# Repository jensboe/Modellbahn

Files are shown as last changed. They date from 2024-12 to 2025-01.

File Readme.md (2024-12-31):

# System architecture
The `adapter board A` is connected to a nucleo 64 board.
The `adapter board A` provides a 
```mermaid
block-beta

columns 1
block:selfmade
    block:base
        columns 1
        nucleo
        adapter["adapter board A"]
    end
    space
    expansion_1["expansion board A 1"]
    space
    expansion_n["expansion board A n"]
    space
    expansion_b["expansion board B"]
    adapter     <--> expansion_1
    expansion_1   ----> expansion_n
    expansion_n  ----> expansion_b
    style expansion_b stroke:#333,stroke-dasharray: 5 5;
end
space
block:extern
    power_supply
    track_1
    switch_1_a
    switch_1_b
    track_x
    switch_y_a
    switch_y_b
end
power_supply --> adapter
expansion_1 --> track_1
expansion_1 --> switch_1_a
expansion_1 --> switch_1_b

expansion_n --> track_x
expansion_n --> switch_y_a
expansion_n --> switch_y_b
```
## Connection between expansion boards
Required Wires:
1. Drive Ground
2. Drive voltage
3. Switch voltage
4. Vcc (3V3 or 5V?)
5. D_Ground
6. MOSI
7. MISO
8. CLK

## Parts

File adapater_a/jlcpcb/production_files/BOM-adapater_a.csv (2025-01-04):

Comment | Designator | Footprint | LCSC | Quantity
CN7 | J104 | PinHeader_2x10_P2.54mm_Vertical | C124359 | 1
Jumper_3_Bridged12 | JP101,JP102,JP103,JP105,JP106 | PinHeader_1x03_P2.54mm_Vertical | C124376 | 5
100k | R301 | R_0805_2012Metric | C149504 | 1
10n | C106,C109,C110,C304,C305 | C_0805_2012Metric | C1710 | 5
1k2 | R102,R302,R303 | R_0805_2012Metric | C17379 | 3
10k | R101,R105,R106 | R_0805_2012Metric | C17414 | 3
150 | R108,R109,R110,R111 | R_0805_2012Metric | C17471 | 4
68k | R104,R112,R113 | R_0805_2012Metric | C17801 | 3
yl | D106 | LED_0805_2012Metric | C2296 | 1
gr | D104,D107 | LED_0805_2012Metric | C2297 | 2
820 | R107 | R_0805_2012Metric | C23253 | 1
0R1 | R103 | R_1206_3216Metric | C25334 | 1
CN10 | J105 | PinHeader_2x17_P2.54mm_Vertical | C2685134 | 1
TLV2372 | U102 | SOIC-8_3.9x4.9mm_P1.27mm | C27204 | 1
100n | C108,C303 | C_0805_2012Metric | C28233 | 2
10u | C105 | CP_Elec_6.3x5.4 | C29199 | 1
KBL406 | D101 | Diode_Bridge_Vishay_KBL | C3078 | 1
SW_DIP_x10 | SW101 | SW_DIP_SPSTx10_Slide_KingTek_DSHP10TS_W7.62mm_P1.27mm | C314500 | 1
220u | C107 | C_Elec_10x10.2 | C3358 | 1
100u | C302 | CP_Elec_6.3x5.4 | C37308 | 1
5n6 | C301 | C_0805_2012Metric | C56078 | 1
CN9 | J103 | PinHeader_2x15_P2.54mm_Vertical | C56496 | 1
B340 | D102,D103 | D_SMA | C64982 | 2
CN8 | J102 | PinHeader_2x08_P2.54mm_Vertical | C68234 | 1
1N4148W | D301,D302 | D_SOD-123 | C81598 | 2
red | D105 | LED_0805_2012Metric | C84256 | 1
4m7 | C101,C102,C103,C104 | CP_Radial_D18.0mm_P7.50mm | C92163 | 4
L6226 | U301 | UFQFPN-32-1EP_5x5mm_P0.5mm_EP3.5x3.5mm | C95357 | 1
Conn_01x03 | J101,J201 | TerminalBlock_4Ucon_1x03_P3.50mm_Vertical | C976557 | 2
Conn_01x06 | J202 | TerminalBlock_4Ucon_1x06_P3.50mm_Vertical | C976560 | 1
TPS5430DDA | U101 | TI_SO-PowerPAD-8_ThermalVias | C9864 | 1
47u | L101 | L_Ferrocore_DLG-0504 | C9889 | 1

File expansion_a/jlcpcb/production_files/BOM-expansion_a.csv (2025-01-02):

Comment | Designator | Footprint | LCSC | Quantity
Jumper_3_Bridged12 | JP1001,JP301,JP401,JP501,JP601,JP701,JP801,JP901 | PinHeader_1x03_P2.54mm_Vertical | C124376 | 8
1k2 | R1002,R302,R402,R502,R602,R702,R802,R902 | R_0805_2012Metric | C17379 | 8
120 | R1001,R301,R401,R501,R601,R701,R801,R901 | R_0805_2012Metric | C17437 | 8
74HC373 | U101 | SO-20_5.3x12.6mm_P1.27mm | C22374060 | 1
100n | C101,C102 | C_0805_2012Metric | C28233 | 2
LED | D1001,D301,D401,D501,D601,D701,D801,D901 | CP_EIA-3528-12_Kemet-T | C5246350 | 8
74HC595 | U102 | SOIC-16W_5.3x10.2mm_P1.27mm | C5947 | 1
GAQY212G1S | U1001,U301,U401,U501,U601,U701,U801,U901 | SO-4_4.4x3.9mm_P2.54mm | C7435108 | 8
Conn_01x03 | J1101,J201 | TerminalBlock_4Ucon_1x03_P3.50mm_Vertical | C976557 | 2
Conn_01x06 | J1102,J202 | TerminalBlock_4Ucon_1x06_P3.50mm_Vertical | C976560 | 2
Conn_01x08 | J101 | TerminalBlock_4Ucon_1x08_P3.50mm_Vertical | C976562 | 1

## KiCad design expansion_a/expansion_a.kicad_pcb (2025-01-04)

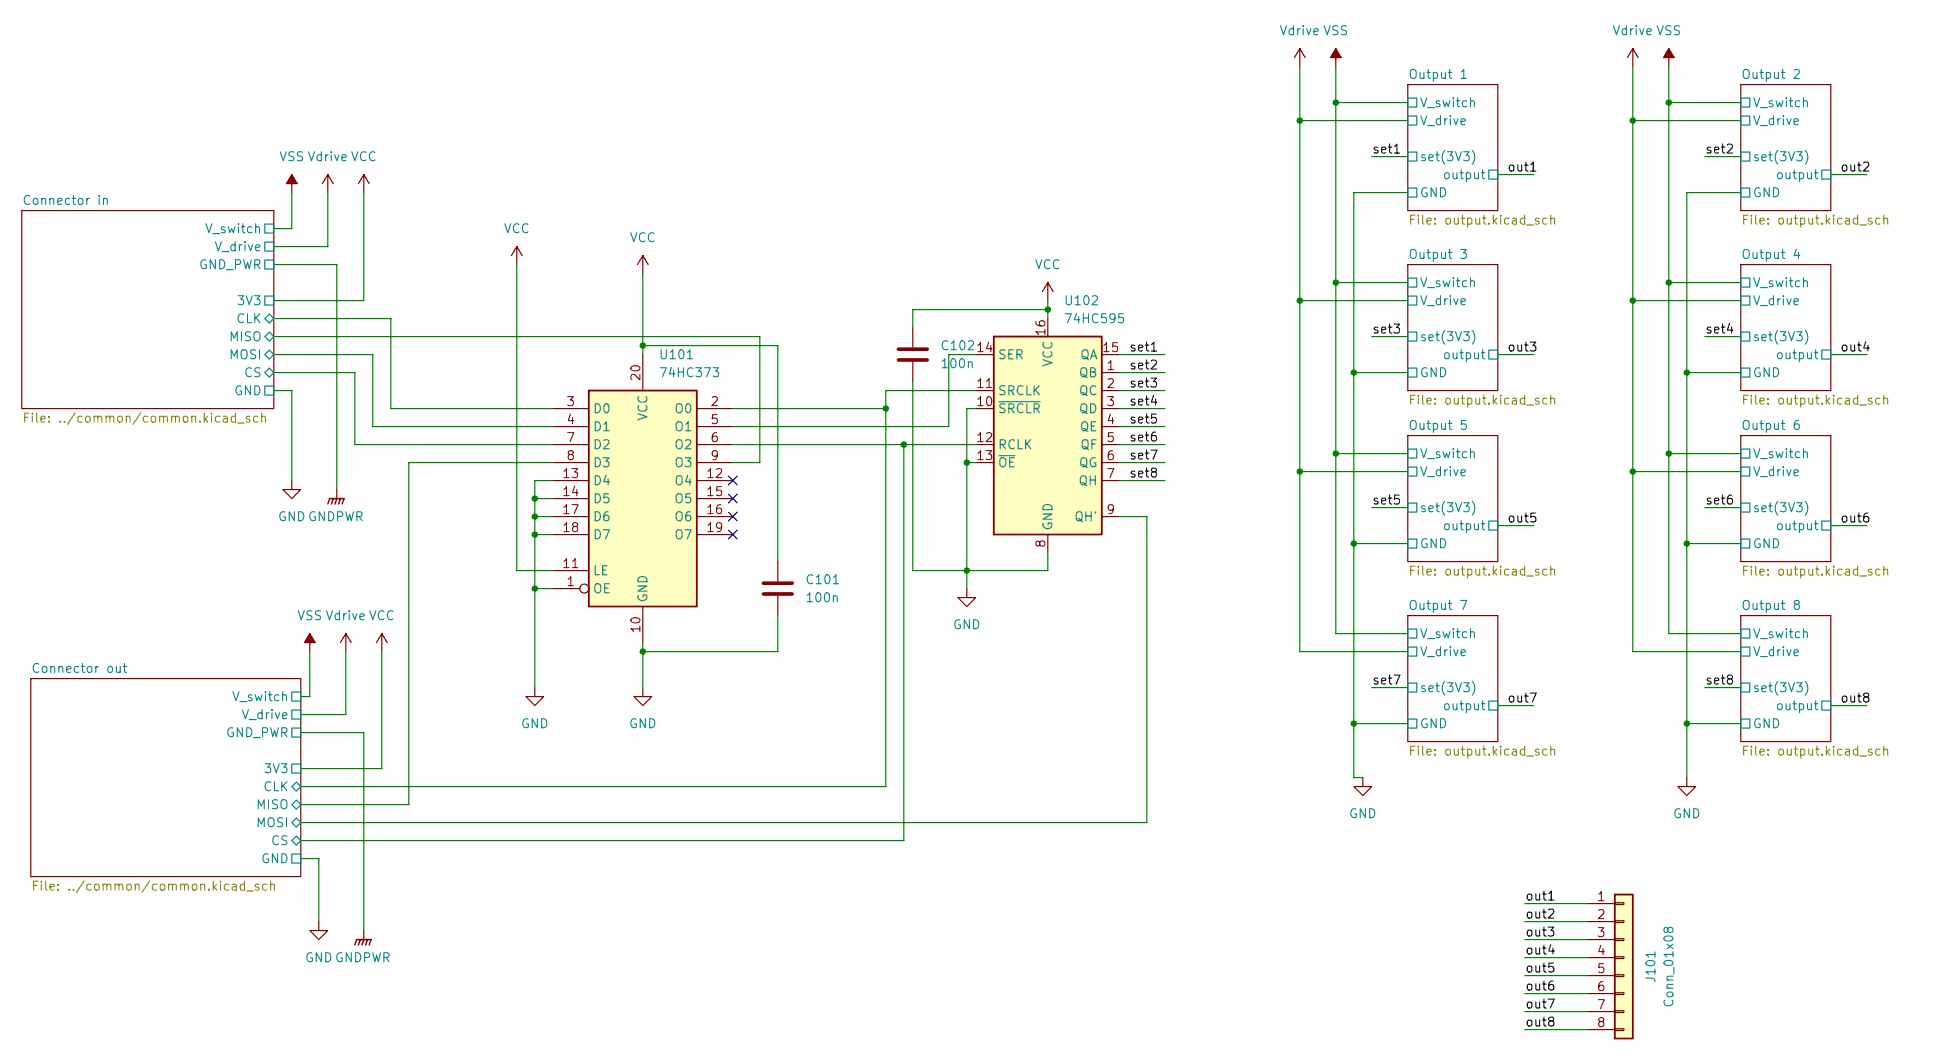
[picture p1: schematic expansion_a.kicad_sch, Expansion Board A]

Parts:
C101, C102: 100n; C_0805_2012Metric; LCSC C28233
J101: Conn_01x08; TerminalBlock_4Ucon_1x08_P3.50mm_Vertical; LCSC C976562
U101: 74HC373; SO-20_5.3x12.6mm_P1.27mm; LCSC C22374060
U102: 74HC595; SOIC-16W_5.3x10.2mm_P1.27mm; LCSC C5947

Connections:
/Connector in/CLK: U101.3 (D0); also elsewhere on the board
/Connector in/CS: U101.7 (D2); also elsewhere on the board
/Connector in/MISO: U101.9 (O3); also elsewhere on the board
/Connector in/MOSI: U101.4 (D1); also elsewhere on the board
/Connector out/CLK: U101.2 (O0), U102.11 (SRCLK); also elsewhere on the board
/Connector out/CS: U101.6 (O2), U102.12 (RCLK); also elsewhere on the board
/Connector out/MISO: U101.8 (D3); also elsewhere on the board
/Connector out/MOSI: U102.9 (QH'); also elsewhere on the board
/out1: J101.1; also elsewhere on the board
/out2: J101.2; also elsewhere on the board
/out3: J101.3; also elsewhere on the board
/out4: J101.4; also elsewhere on the board
/out5: J101.5; also elsewhere on the board
/out6: J101.6; also elsewhere on the board
/out7: J101.7; also elsewhere on the board
/out8: J101.8; also elsewhere on the board
/set1: U102.15 (QA); also elsewhere on the board
/set2: U102.1 (QB); also elsewhere on the board
/set3: U102.2 (QC); also elsewhere on the board
/set4: U102.3 (QD); also elsewhere on the board
/set5: U102.4 (QE); also elsewhere on the board
/set6: U102.5 (QF); also elsewhere on the board
/set7: U102.6 (QG); also elsewhere on the board
/set8: U102.7 (QH); also elsewhere on the board
GND: C101.2, C102.2, U101.1 (OE), U101.10 (GND), U101.13 (D4), U101.14 (D5), U101.17 (D6), U101.18 (D7), U102.8 (GND), U102.10 (~SRCLR), U102.13 (~OE); also elsewhere on the board
unnamed: U101.5 (O1), U102.14 (SER)
VCC: C101.1, C102.1, U101.11 (LE), U101.20 (VCC), U102.16 (VCC); also elsewhere on the board

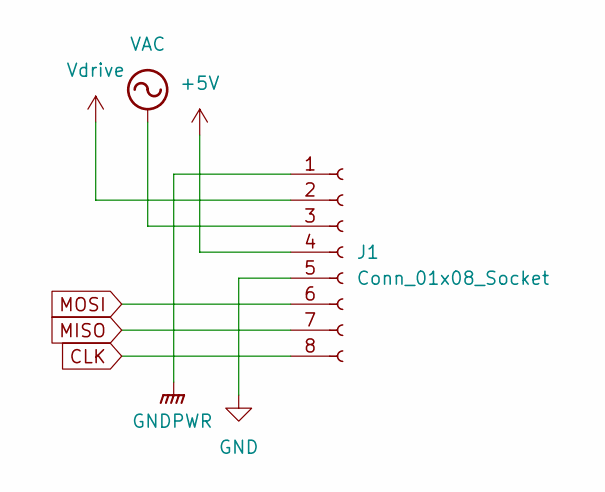
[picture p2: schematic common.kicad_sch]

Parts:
J1: Conn_01x08_Socket; TerminalBlock_4Ucon_1x08_P3.50mm_Vertical; LCSC C976562

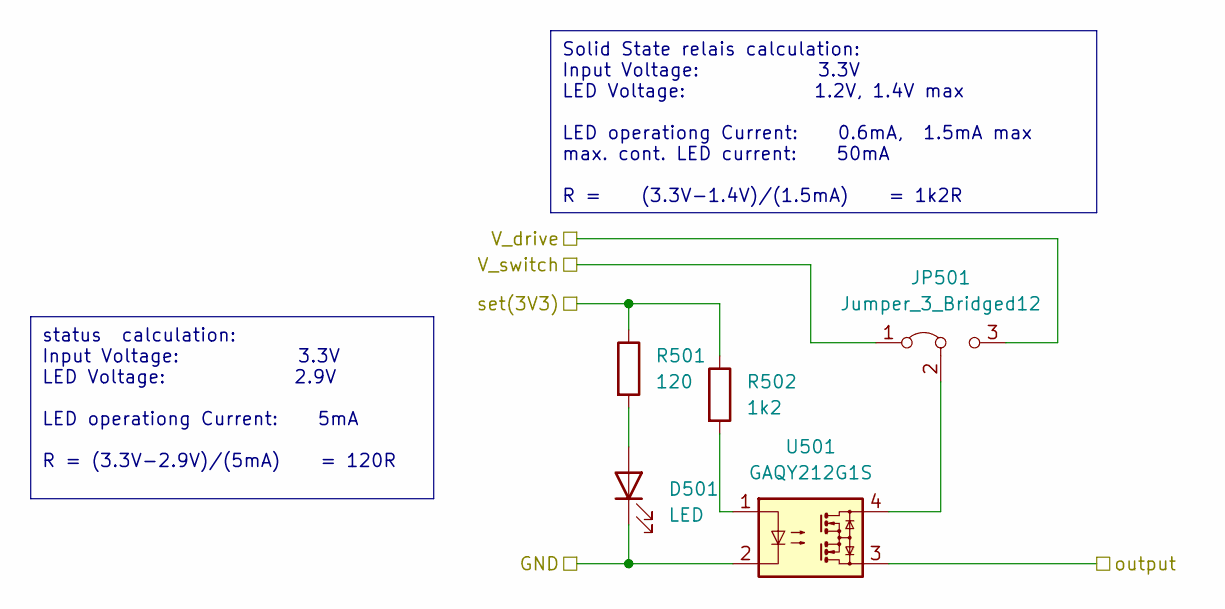
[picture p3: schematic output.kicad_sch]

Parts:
D501: LED; CP_EIA-3528-12_Kemet-T; LCSC C2290
JP501: Jumper_3_Bridged12; PinHeader_1x03_P2.54mm_Vertical; LCSC C124376
R501: 120; R_0805_2012Metric; LCSC C17437
R502: 1k2; R_0805_2012Metric; LCSC C17379
U501: GAQY212G1S; SO-4_4.4x3.9mm_P2.54mm; LCSC C7435108

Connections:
/out3: U501.3; also elsewhere on the board
/set3: R501.1, R502.1; also elsewhere on the board
GND: D501.1 (K), U501.2; also elsewhere on the board
unnamed: D501.2 (A), R501.2
unnamed: JP501.2 (C), U501.4
unnamed: R502.2, U501.1
VSS: JP501.1 (A); also elsewhere on the board
Vdrive: JP501.3 (B); also elsewhere on the board

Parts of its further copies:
D301, D401, D601, D701, D801, D901, D1001: LED; CP_EIA-3528-12_Kemet-T; LCSC C2290
JP301, JP401, JP601, JP701, JP801, JP901, JP1001: Jumper_3_Bridged12; PinHeader_1x03_P2.54mm_Vertical; LCSC C124376
R301, R401, R601, R701, R801, R901, R1001: 120; R_0805_2012Metric; LCSC C17437
R302, R402, R602, R702, R802, R902, R1002: 1k2; R_0805_2012Metric; LCSC C17379
U301, U401, U601, U701, U801, U901, U1001: GAQY212G1S; SO-4_4.4x3.9mm_P2.54mm; LCSC C7435108

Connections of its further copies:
/out1: U301.3; also elsewhere on the board
/out2: U401.3; also elsewhere on the board
/out4: U601.3; also elsewhere on the board
/out5: U701.3; also elsewhere on the board
/out6: U801.3; also elsewhere on the board
/out7: U901.3; also elsewhere on the board
/out8: U1001.3; also elsewhere on the board
/set1: R301.1, R302.1; also elsewhere on the board
/set2: R401.1, R402.1; also elsewhere on the board
/set4: R601.1, R602.1; also elsewhere on the board
/set5: R701.1, R702.1; also elsewhere on the board
/set6: R801.1, R802.1; also elsewhere on the board
/set7: R901.1, R902.1; also elsewhere on the board
/set8: R1001.1, R1002.1; also elsewhere on the board
GND: D301.1 (K), D401.1 (K), D601.1 (K), D701.1 (K), D801.1 (K), D901.1 (K), D1001.1 (K), U301.2, U401.2, U601.2, U701.2, U801.2, U901.2, U1001.2; also elsewhere on the board
unnamed: D301.2 (A), R301.2
unnamed: D401.2 (A), R401.2
unnamed: D601.2 (A), R601.2
unnamed: D701.2 (A), R701.2
unnamed: D801.2 (A), R801.2
unnamed: D901.2 (A), R901.2
unnamed: D1001.2 (A), R1001.2
unnamed: JP301.2 (C), U301.4
unnamed: JP401.2 (C), U401.4
unnamed: JP601.2 (C), U601.4
unnamed: JP701.2 (C), U701.4
unnamed: JP801.2 (C), U801.4
unnamed: JP901.2 (C), U901.4
unnamed: JP1001.2 (C), U1001.4
unnamed: R302.2, U301.1
unnamed: R402.2, U401.1
unnamed: R602.2, U601.1
unnamed: R702.2, U701.1
unnamed: R802.2, U801.1
unnamed: R902.2, U901.1
unnamed: R1002.2, U1001.1
VSS: JP301.1 (A), JP401.1 (A), JP601.1 (A), JP701.1 (A), JP801.1 (A), JP901.1 (A), JP1001.1 (A); also elsewhere on the board
Vdrive: JP301.3 (B), JP401.3 (B), JP601.3 (B), JP701.3 (B), JP801.3 (B), JP901.3 (B), JP1001.3 (B); also elsewhere on the board

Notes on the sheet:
Solid State relais calculation: Input Voltage: 3.3V LED Voltage: 1.2V, 1.4V max LED operationg Current: 0.6mA, 1.5mA max max. cont. LED current: 50mA R = (3.3V-1.4V)/(1.5mA) = 1k2R
status calculation: Input Voltage: 3.3V LED Voltage: 2.9V LED operationg Current: 5mA R = (3.3V-2.9V)/(5mA) = 120R

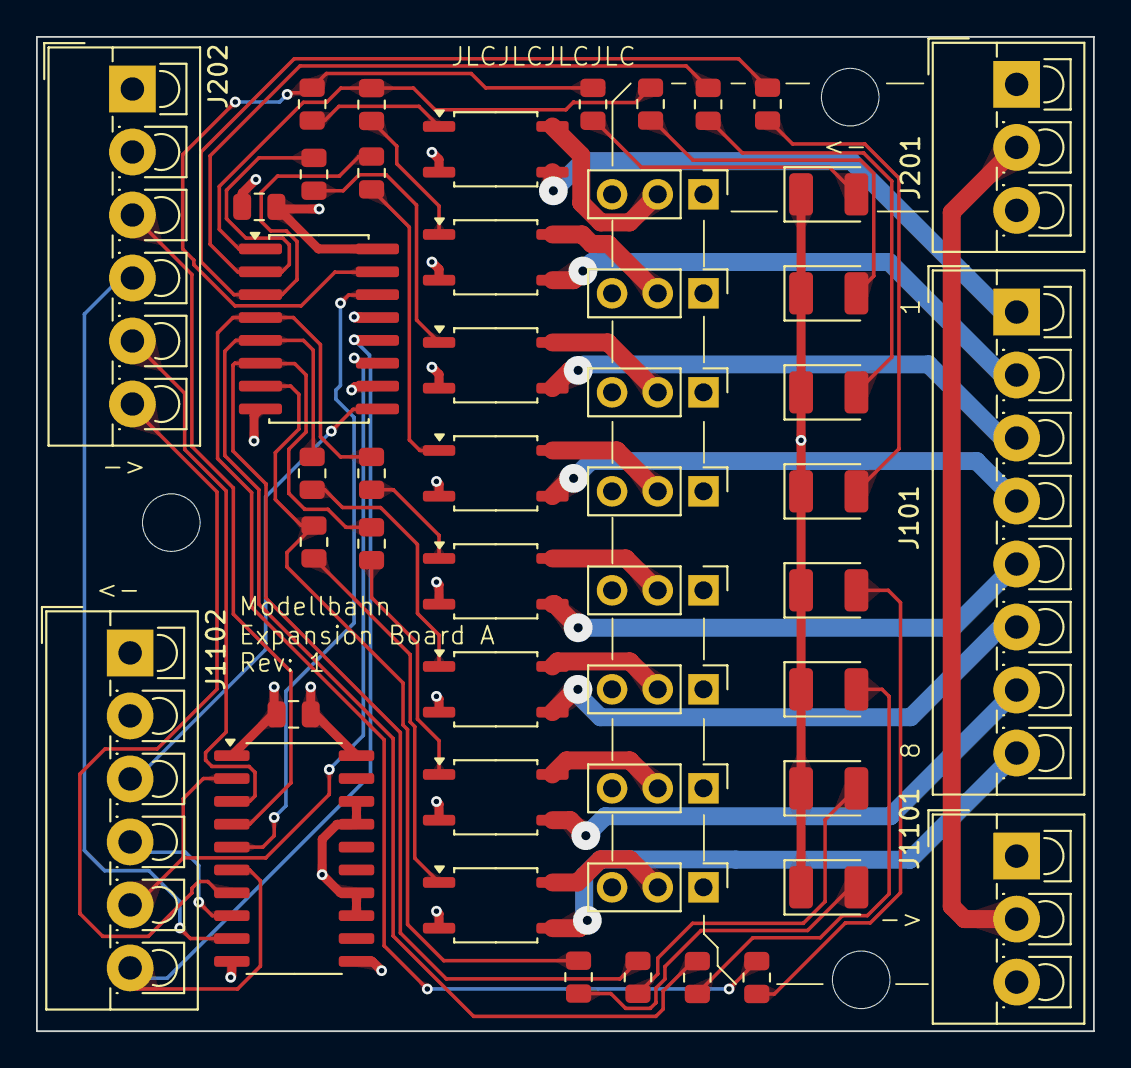
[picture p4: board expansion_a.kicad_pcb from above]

Board: 4 copper layers, 58.7 x 55.2 mm, 52 parts (0 on the bottom side), 54 nets.

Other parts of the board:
J201, J1101: Conn_01x03; TerminalBlock_4Ucon_1x03_P3.50mm_Vertical
J202, J1102: Conn_01x06; TerminalBlock_4Ucon_1x06_P3.50mm_Vertical
REF1, REF2, REF3: MountingHole_3.2mm_M3

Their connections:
/Connector in/CLK: J202.5; also elsewhere on the board
/Connector in/CS: J202.6; also elsewhere on the board
/Connector in/MISO: J202.4; also elsewhere on the board
/Connector in/MOSI: J202.3; also elsewhere on the board
/Connector out/CLK: J1102.5; also elsewhere on the board
/Connector out/CS: J1102.6; also elsewhere on the board
/Connector out/MISO: J1102.4; also elsewhere on the board
/Connector out/MOSI: J1102.3; also elsewhere on the board
GND: J202.2, J1102.2; also elsewhere on the board
GNDPWR: J201.2, J1101.2
VCC: J202.1, J1102.1; also elsewhere on the board
VSS: J201.3, J1101.3; also elsewhere on the board
Vdrive: J201.1, J1101.1; also elsewhere on the board

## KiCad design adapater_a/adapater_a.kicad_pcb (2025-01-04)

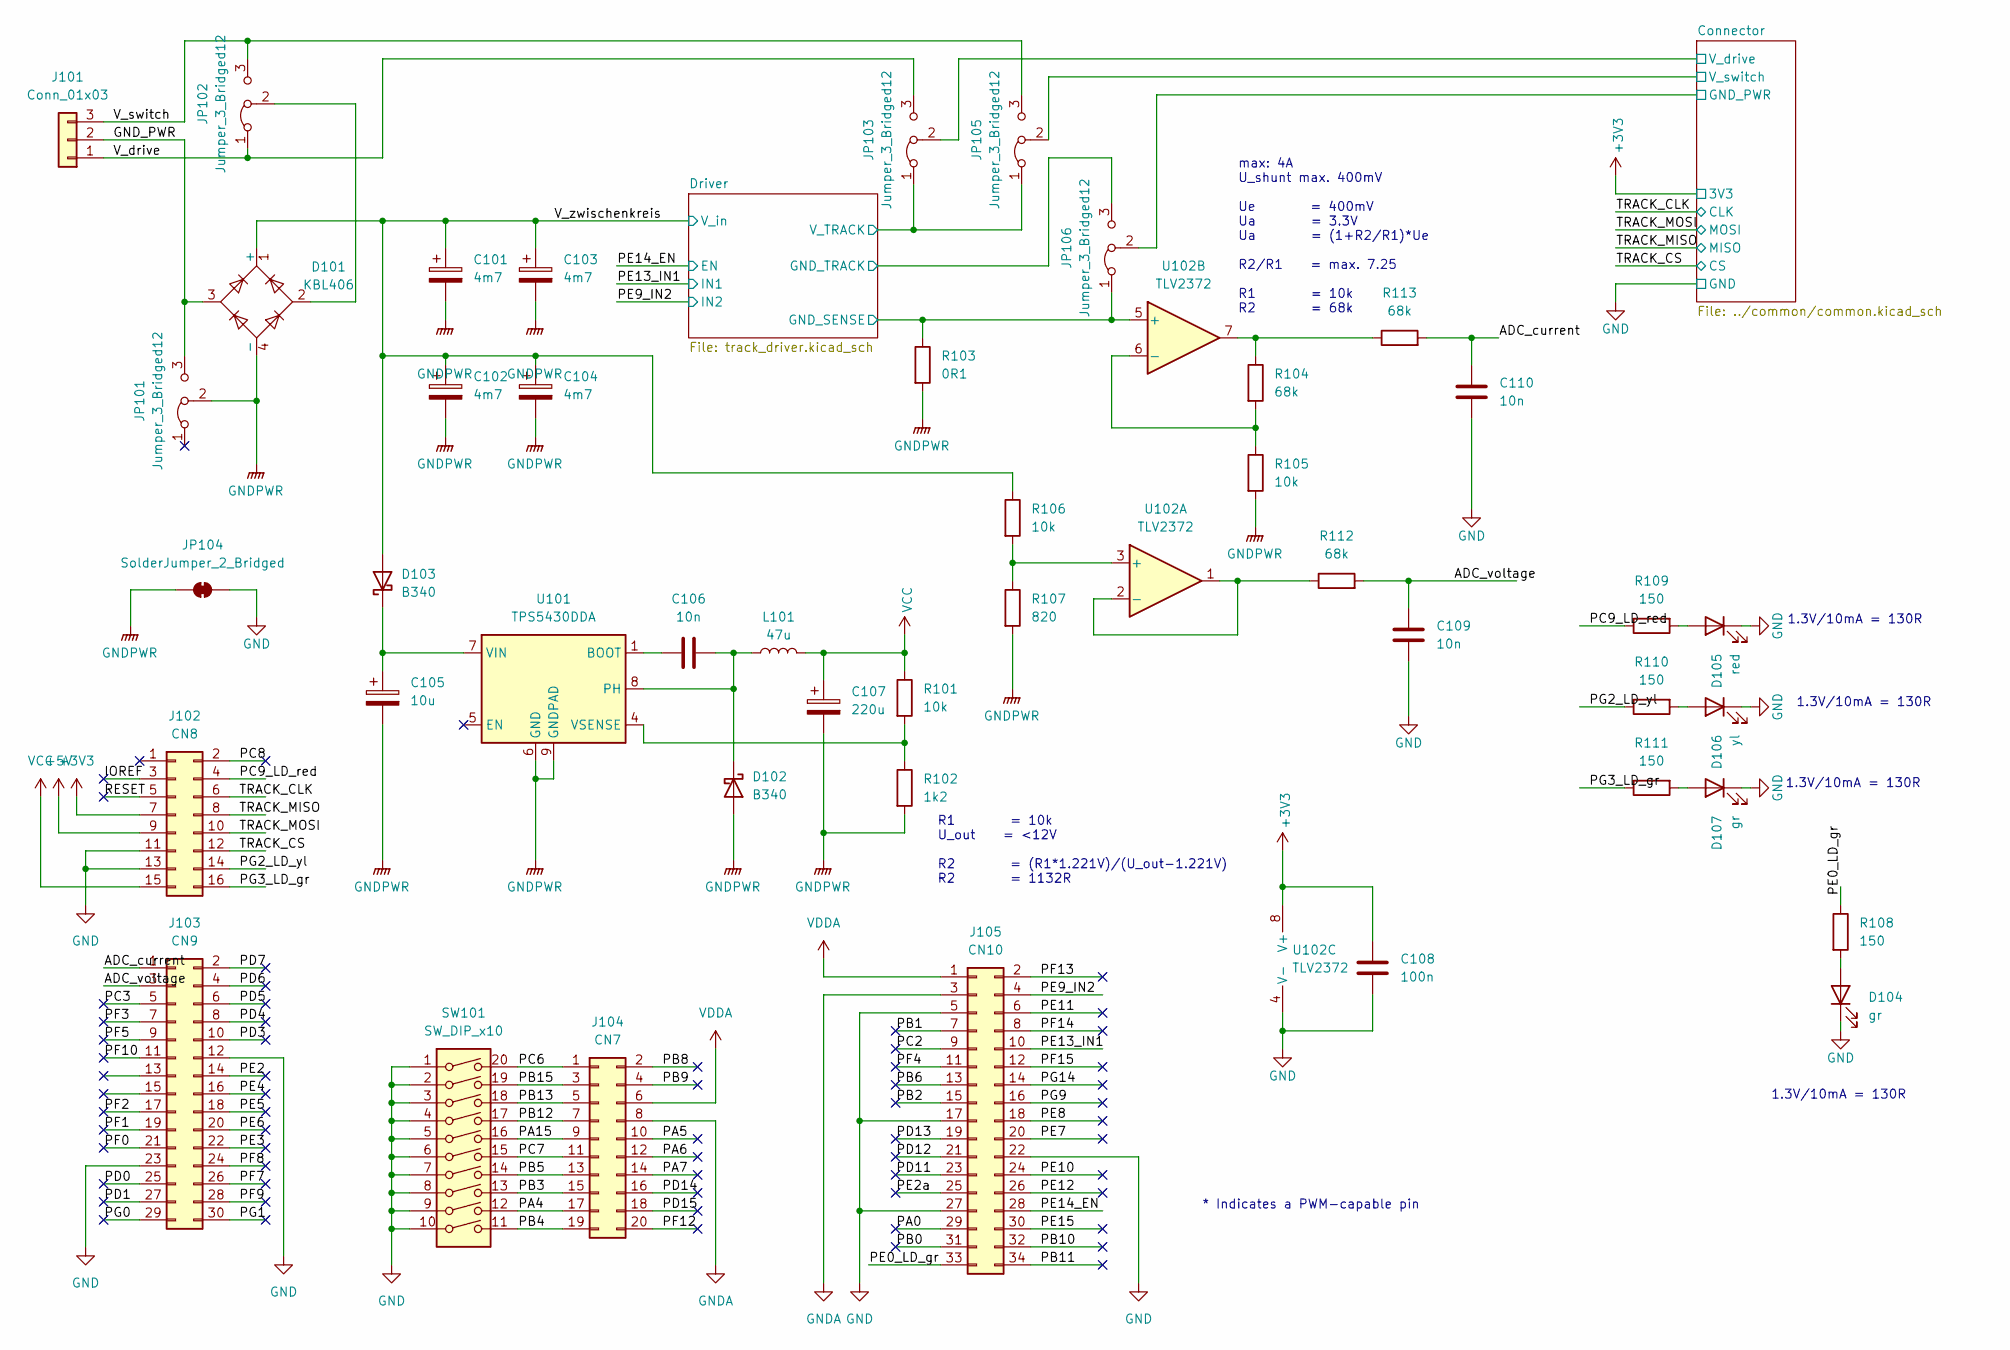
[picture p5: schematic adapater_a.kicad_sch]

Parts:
C101, C102, C103, C104: 4m7; CP_Radial_D18.0mm_P7.50mm; LCSC C92163
C105: 10u; CP_Elec_6.3x5.4; LCSC C29199
C106, C109, C110: 10n; C_0805_2012Metric; LCSC C1710
C107: 220u; C_Elec_10x10.2; LCSC C3358
C108: 100n; C_0805_2012Metric; LCSC C28233
D101: KBL406; Diode_Bridge_Vishay_KBL; LCSC C3078
D102, D103: B340; D_SMA; LCSC C64982
D104, D107: gr; LED_0805_2012Metric; LCSC C2297
D105: red; LED_0805_2012Metric; LCSC C84256
D106: yl; LED_0805_2012Metric; LCSC C2296
J101: Conn_01x03; TerminalBlock_4Ucon_1x03_P3.50mm_Vertical; LCSC C976557
J102: CN8; PinHeader_2x08_P2.54mm_Vertical; LCSC C68234
J103: CN9; PinHeader_2x15_P2.54mm_Vertical; LCSC C56496
J104: CN7; PinHeader_2x10_P2.54mm_Vertical; LCSC C5116480
J105: CN10; PinHeader_2x17_P2.54mm_Vertical; LCSC C2685134
JP101, JP102, JP103, JP105, JP106: Jumper_3_Bridged12; PinHeader_1x03_P2.54mm_Vertical; LCSC C124376
JP104: SolderJumper_2_Bridged; SolderJumper-2_P1.3mm_Bridged_RoundedPad1.0x1.5mm
L101: 47u; L_Ferrocore_DLG-0504; LCSC C9889
R101, R105, R106: 10k; R_0805_2012Metric; LCSC C17414
R102: 1k2; R_0805_2012Metric; LCSC C17379
R103: 0R1; R_1206_3216Metric; LCSC C25334
R104, R112, R113: 68k; R_0805_2012Metric; LCSC C17801
R107: 820; R_0805_2012Metric; LCSC C23253
R108, R109, R110, R111: 150; R_0805_2012Metric; LCSC C17471
SW101: SW_DIP_x10; SW_DIP_SPSTx10_Slide_KingTek_DSHP10TS_W7.62mm_P1.27mm; LCSC C314500
U101: TPS5430DDA; TI_SO-PowerPAD-8_ThermalVias; LCSC C9864
U102: TLV2372; SOIC-8_3.9x4.9mm_P1.27mm; LCSC C27204

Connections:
+3V3: C108.1, J102.7, U102.8 (V+); also elsewhere on the board
+5V: J102.9
/ADC_current: C110.2, J103.1, R113.2
/ADC_voltage: C109.2, J103.3, R112.2
/Connector/GND_PWR: JP106.2 (C); also elsewhere on the board
/Connector/V_drive: JP103.2 (C); also elsewhere on the board
/Connector/V_switch: JP105.2 (C); also elsewhere on the board
/Driver/GND_SENSE: JP106.1 (A), R103.1, U102.5 (+); also elsewhere on the board
/Driver/GND_TRACK: JP106.3 (B); also elsewhere on the board
/Driver/V_TRACK: JP103.1 (A), JP105.1 (A); also elsewhere on the board
/GND_PWR: D101.3, J101.2, JP101.3 (B)
/IOREF: J102.3
/PA0: J105.29
/PA4: J104.17, SW101.12
/PA5: J104.10
/PA6: J104.12
/PA7: J104.14
/PA15: J104.9, SW101.16
/PB0: J105.31
/PB1: J105.7
/PB2: J105.15
/PB3: J104.15, SW101.13
/PB4: J104.19, SW101.11
/PB5: J104.13, SW101.14
/PB6: J105.13
/PB8: J104.2
/PB9: J104.4
/PB10: J105.32
/PB11: J105.34
/PB12: J104.7, SW101.17
/PB13: J104.5, SW101.18
/PB15: J104.3, SW101.19
/PC2: J105.9
/PC3: J103.5
/PC6: J104.1, SW101.20
/PC7: J104.11, SW101.15
/PC8: J102.2
/PC9_LD_red: J102.4, R109.1
/PD0: J103.25
/PD1: J103.27
/PD3: J103.10
/PD4: J103.8
/PD5: J103.6
/PD6: J103.4
/PD7: J103.2
/PD11: J105.23
/PD12: J105.21
/PD13: J105.19
/PD14: J104.16
/PD15: J104.18
/PE0_LD_gr: J105.33, R108.1
/PE2: J103.14
/PE2a: J105.25
/PE3: J103.22
/PE4: J103.16
/PE5: J103.18
/PE6: J103.20
/PE7: J105.20
/PE8: J105.18
/PE9_IN2: J105.4; also elsewhere on the board
/PE10: J105.24
/PE11: J105.6
/PE12: J105.26
/PE13_IN1: J105.10; also elsewhere on the board
/PE14_EN: J105.28; also elsewhere on the board
/PE15: J105.30
/PF0: J103.21
/PF1: J103.19
/PF2: J103.17
/PF3: J103.7
/PF4: J105.11
/PF5: J103.9
/PF7: J103.26
/PF8: J103.24
/PF9: J103.28
/PF10: J103.11
/PF12: J104.20
/PF13: J105.2
/PF14: J105.8
/PF15: J105.12
/PG0: J103.29
/PG1: J103.30
/PG2_LD_yl: J102.14, R110.1
/PG3_LD_gr: J102.16, R111.1
/PG9: J105.16
/PG14: J105.14
/RESET: J102.5
/TRACK_CLK: J102.6; also elsewhere on the board
/TRACK_CS: J102.12; also elsewhere on the board
/TRACK_MISO: J102.8; also elsewhere on the board
/TRACK_MOSI: J102.10; also elsewhere on the board
/V_drive: J101.1, JP102.1 (A), JP103.3 (B)
/V_switch: J101.3, JP102.3 (B), JP105.3 (B)
/V_zwischenkreis: C101.1, C102.1, C103.1, C104.1, D101.1 (+), D103.2 (A), R106.1; also elsewhere on the board
GND: C108.2, C109.1, C110.1, D104.1 (K), D105.1 (K), D106.1 (K), D107.1 (K), J102.11, J102.13, J103.12, J103.23, J105.5, J105.17, J105.22, J105.27, JP104.2 (B), SW101.1, SW101.2, SW101.3, SW101.4, SW101.5, SW101.6, SW101.7, SW101.8, SW101.9, SW101.10, U102.4 (V-); also elsewhere on the board
GNDA: J104.8, J105.3
GNDPWR: C101.2, C102.2, C103.2, C104.2, C105.2, C107.2, D101.4 (-), D102.2 (A), JP101.2 (C), JP104.1 (A), R102.2, R103.2, R105.2, R107.2, U101.6 (GND), U101.9 (GNDPAD); also elsewhere on the board
unnamed: C106.2, D102.1 (K), L101.1, U101.8 (PH)
unnamed: C105.1, D103.1 (K), U101.7 (VIN)
unnamed: D104.2 (A), R108.2
unnamed: D105.2 (A), R109.2
unnamed: D106.2 (A), R110.2
unnamed: D107.2 (A), R111.2
unnamed: D101.2, JP102.2 (C)
unnamed: R104.1, R113.1, U102.7
unnamed: C106.1, U101.1 (BOOT)
unnamed: R101.2, R102.1, U101.4 (VSENSE)
unnamed: R106.2, R107.1, U102.3 (+)
unnamed: R112.1, U102.1, U102.2 (-)
unnamed: R104.2, R105.1, U102.6 (-)
VCC: C107.1, J102.15, L101.2, R101.1
VDDA: J104.6, J105.1

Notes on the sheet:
1.3V/10mA = 130R
R1 = 10k U_out = <12V R2 = (R1*1.221V)/(U_out-1.221V) R2 = 1132R
max: 4A U_shunt max. 400mV Ue = 400mV Ua = 3.3V Ua = (1+R2/R1)*Ue R2/R1 = max. 7.25 R1 = 10k R2 = 68k
* Indicates a PWM-capable pin

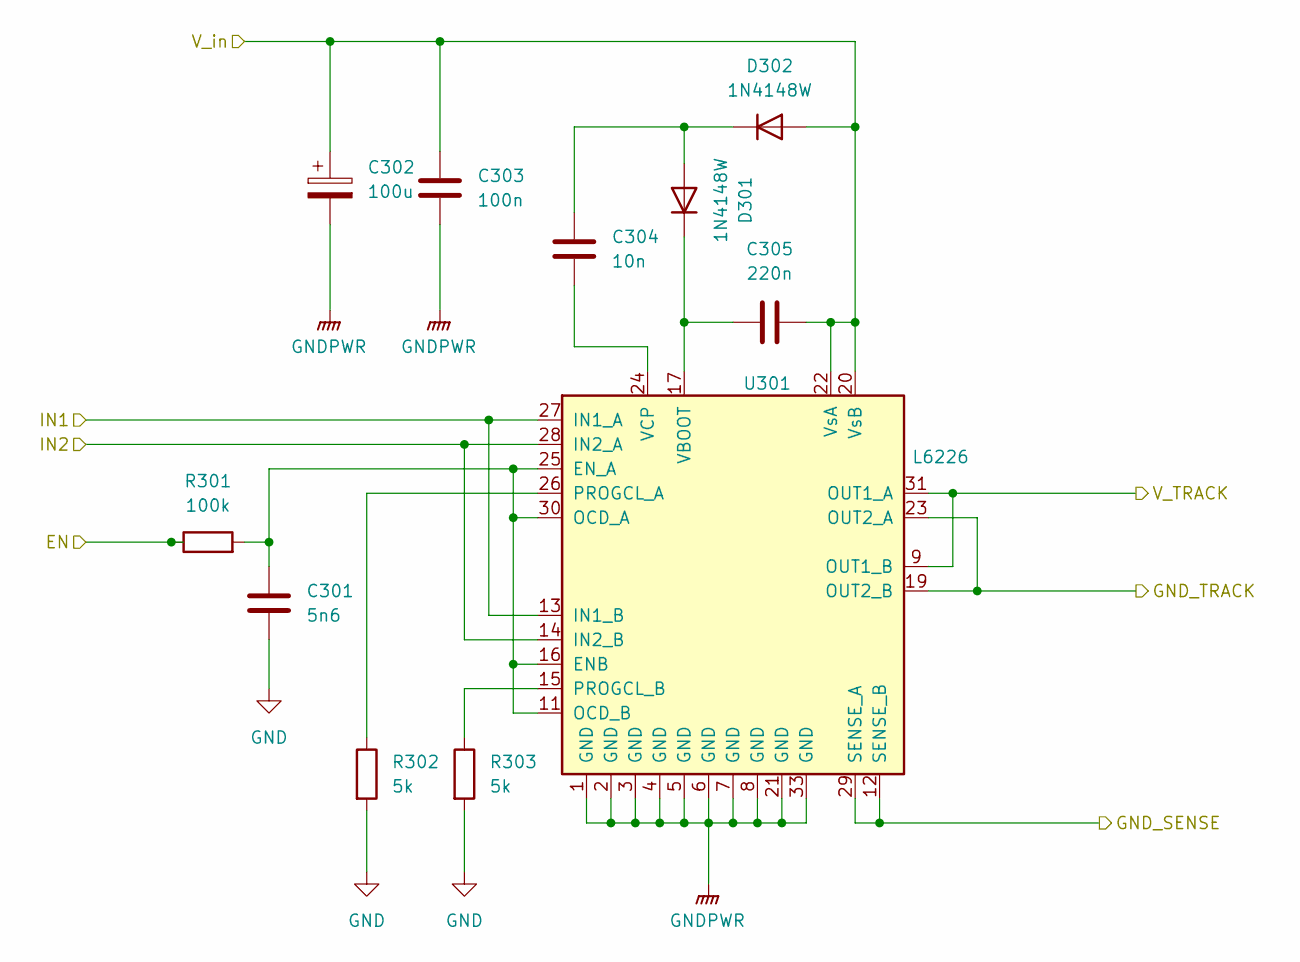
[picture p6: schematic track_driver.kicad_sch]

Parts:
C301: 5n6; C_0805_2012Metric; LCSC C56078
C302: 100u; CP_Elec_6.3x5.4; LCSC C37308
C303: 100n; C_0805_2012Metric; LCSC C28233
C304: 10n; C_0805_2012Metric; LCSC C1710
C305: 220n; C_0805_2012Metric; LCSC C1710
D301, D302: 1N4148W; D_SOD-123; LCSC C81598
R301: 100k; R_0805_2012Metric; LCSC C149504
R302, R303: 5k; R_0805_2012Metric; LCSC C17379
U301: L6226; UFQFPN-32-1EP_5x5mm_P0.5mm_EP3.5x3.5mm; LCSC C95357

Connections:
/Driver/GND_SENSE: U301.12 (SENSE_B), U301.29 (SENSE_A); also elsewhere on the board
/Driver/GND_TRACK: U301.19 (OUT2_B), U301.23 (OUT2_A); also elsewhere on the board
/Driver/V_TRACK: U301.9 (OUT1_B), U301.31 (OUT1_A); also elsewhere on the board
/PE9_IN2: U301.14 (IN2_B), U301.28 (IN2_A); also elsewhere on the board
/PE13_IN1: U301.13 (IN1_B), U301.27 (IN1_A); also elsewhere on the board
/PE14_EN: R301.1; also elsewhere on the board
/V_zwischenkreis: C302.1, C303.1, C305.2, D302.2 (A), U301.20 (VsB), U301.22 (VsA); also elsewhere on the board
GND: C301.2, R302.2, R303.2; also elsewhere on the board
GNDPWR: C302.2, C303.2, U301.1 (GND), U301.2 (GND), U301.3 (GND), U301.4 (GND), U301.5 (GND), U301.6 (GND), U301.7 (GND), U301.8 (GND), U301.21 (GND), U301.33 (GND); also elsewhere on the board
unnamed: C304.1, D301.2 (A), D302.1 (K)
unnamed: C305.1, D301.1 (K), U301.17 (VBOOT)
unnamed: C301.1, R301.2, U301.11 (OCD_B), U301.16 (ENB), U301.25 (EN_A), U301.30 (OCD_A)
unnamed: R302.1, U301.26 (PROGCL_A)
unnamed: R303.1, U301.15 (PROGCL_B)
unnamed: C304.2, U301.24 (VCP)


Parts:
J1: Conn_01x08_Socket; TerminalBlock_4Ucon_1x08_P3.50mm_Vertical; LCSC C976562

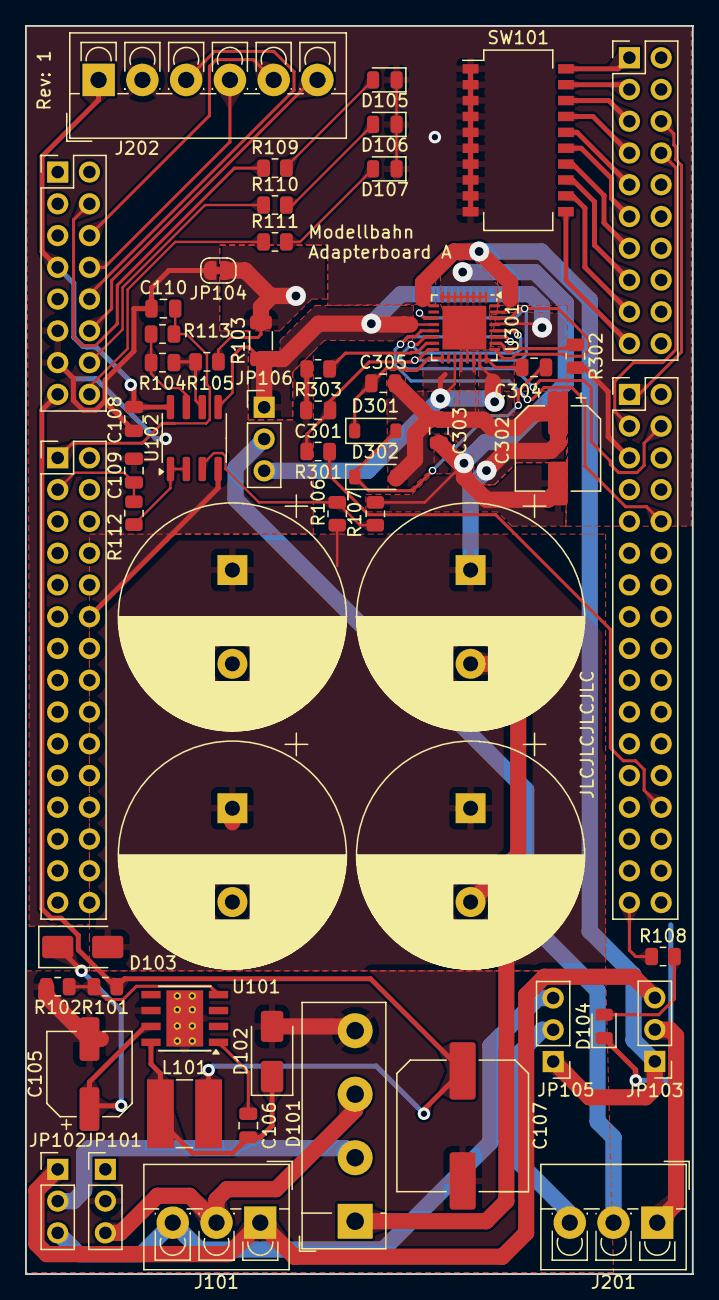
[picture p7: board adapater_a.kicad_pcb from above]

Board: 2 copper layers, 53.3 x 99.8 mm, 58 parts (0 on the bottom side), 58 nets.

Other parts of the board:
J201: Conn_01x03; TerminalBlock_4Ucon_1x03_P3.50mm_Vertical
J202: Conn_01x06; TerminalBlock_4Ucon_1x06_P3.50mm_Vertical

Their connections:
+3V3: J202.1; also elsewhere on the board
/Connector/GND_PWR: J201.2; also elsewhere on the board
/Connector/V_drive: J201.1; also elsewhere on the board
/Connector/V_switch: J201.3; also elsewhere on the board
/TRACK_CLK: J202.5; also elsewhere on the board
/TRACK_CS: J202.6; also elsewhere on the board
/TRACK_MISO: J202.4; also elsewhere on the board
/TRACK_MOSI: J202.3; also elsewhere on the board
GND: J202.2; also elsewhere on the board

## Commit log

2024-12-31 Add nucleo expander board and schematic
    [Modellbahn.kicad_pcb, Modellbahn.kicad_sch]
2024-12-31 Set doc properties, ignore backups
    [Modellbahn.kicad_sch]
2024-12-31 Remove main project
    [Modellbahn.kicad_pcb, Modellbahn.kicad_sch]
2024-12-31 Add project for expansion board
    [expansion_a.kicad_pcb, expansion_a.kicad_sch]
2024-12-31 Add common project for chared ressources
    [common.kicad_pcb, common.kicad_sch]
2024-12-31 Add project for adapter a
    [adapater_a.kicad_pcb, adapater_a.kicad_sch]
2024-12-31 Add common connector
    [common.kicad_pcb, common.kicad_sch]
2024-12-31 Ignore old schematics
2024-12-31 expansion schematics added
    [common.kicad_sch, expansion_a.kicad_pcb, expansion_a.kicad_sch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]
2024-12-31 Error free expansion board
    [common.kicad_sch, expansion_a.kicad_pcb, output.kicad_sch]
2024-12-31 expansion schematic error free
    [expansion_a.kicad_sch, output.kicad_sch]
2025-01-01 Finalise expansion A.
    [common.kicad_sch, expansion_a.kicad_pcb, output.kicad_sch]
2025-01-01 Expander Final II
    [common.kicad_sch, expansion_a.kicad_pcb, expansion_a.kicad_sch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]
2025-01-01 Add JLCPC Tools production data output
    [BOM-expansion_a.csv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]
2025-01-01 Remove right angle in GND wire.
    [expansion_a-CuBottom.gbr, expansion_a-CuIn1.gbr, expansion_a-CuIn2.gbr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]
2025-01-01 Rotate parts according to JLC §D view
    [CPL-expansion_a.csv, expansion_a-CuBottom.gbr, expansion_a-CuIn1.gbr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]
2025-01-01 Rename common "+5V" to "3V3"
    [common.kicad_sch, expansion_a.kicad_pcb, expansion_a.kicad_sch]
2025-01-02 Add capacitors for ic
    [BOM-expansion_a.csv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]
2025-01-02 Silk screen improvments
    [common.kicad_sch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]
2025-01-02 Add first version of adpater A
    [BOM-adapater_a.csv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]
2025-01-02 Realgin nucleo connection
    [adapater_a.kicad_pcb]
2025-01-02 Add voltage messurement
    [adapater_a.kicad_pcb, adapater_a.kicad_sch]
2025-01-04 Update adapter A
    [adapater_a.kicad_pcb, adapater_a.kicad_sch]
2025-01-04 Add missing trace for zwischenkreis
    [adapater_a.kicad_pcb]
2025-01-04 Nicer signal names
    [adapater_a.kicad_pcb, adapater_a.kicad_sch]
2025-01-04 adapter A: Generate production files
    [BOM-adapater_a.csv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]
2025-01-04 State of production
    [CPL-adapater_a.csv, CPL-expansion_a.csv, adapater_a-CuBottom.gbr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]
2025-01-04 Update Expansion board A
    [expansion_a.kicad_pcb]
